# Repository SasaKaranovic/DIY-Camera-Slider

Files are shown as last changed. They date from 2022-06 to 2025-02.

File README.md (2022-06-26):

# DIY WiFi Enabled Camera Slider

## What is this project about?
DIY WiFi Enabled Camera Slider (https://youtu.be/-t66ZylGClk "DIY WiFi Enabled Camera Slider")

Above video shows the finished Camera Slider, how it works, how to build one and motivation behind some of the design decisions.

## How can I build my own?
The above video explains the idea and how hardware and firmware works. It's recommended that you watch that first.
Hardware and firmware build instructions and source files are available in their respective folders.

---

Blog page: https://sasakaranovic.com/projects/diy-camera-slider/

YouTube video: http://www.youtube.com/watch?v=-t66ZylGClk

---

#### Sasa Karanovic

<a href="https://sasakaranovic.com/" target="_blank" title="Sasa Karanovic Home Page"> Home Page</a> &nbsp;&middot;&nbsp;
<a href="https://youtube.com/c/sasakaranovic" target="_blank" title="Sasa Karanovic on YouTube"> YouTube</a> &nbsp;&middot;&nbsp;
<a href="https://github.com/sasakaranovic" target="_blank" title="Sasa Karanovic on GitHub"> GitHub</a> &nbsp;&middot;&nbsp;
<a href="https://twitter.com/_sasakaranovic_" target="_blank" title="Sasa Karanovic on Twitter"> Twitter</a> &nbsp;&middot;&nbsp;
<a href="https://instagram.com/_sasakaranovic_" target="_blank" title="Sasa Karanovic on Instagram"> Instagram</a> &nbsp;&middot;&nbsp;
<a href="https://buymeacoffee.com/sasakaranovic" target="_blank" title="Sasa Karanovic on Buy me a coffee"> Buy me a coffee</a>

[home]: https://raw.githubusercontent.com/SasaKaranovic/common/master/assets/img_home.png "Sasa Karanovic Home Page"
[youtube]: https://raw.githubusercontent.com/SasaKaranovic/common/master/assets/img_youtube.png "Sasa Karanovic YouTube channel"
[github]: https://raw.githubusercontent.com/SasaKaranovic/common/master/assets/img_github.png "Sasa Karanovic on GitHub"
[twitter]: https://raw.githubusercontent.com/SasaKaranovic/common/master/assets/img_twitter.png "Sasa Karanovic on Twitter"
[instagram]: https://raw.githubusercontent.com/SasaKaranovic/common/master/assets/img_instagram.png "Sasa Karanovic on Instagram"
[coffee]: https://raw.githubusercontent.com/SasaKaranovic/common/master/assets/img_coffee.png "Buy me a coffee"

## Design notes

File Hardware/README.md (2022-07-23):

# Driver PCB

We are trying to use off-the-shelf components wherever possible to make this open-source open-hardware project accessible to everyone.
The custom PCB is optional. Manufacturing files are in `Manufacturing files` folder. Source files are in `Altium Source Files` which you could use to modify the design.

## Active BOM

If you decide to build the PCB, you can follow the [Active BOM](https://sasakaranovic.com/activebom/diy-camera-slider.html) to help you visualize where
each component is placed and help during assembly.

## Part list

Below parts you can order online from AliExpress, eBay etc.
Links are provided for reference. Feel free to do your own search and find better quality or price.

- 1x [2020 Aluminium Extrusion](https://www.aliexpress.com/item/33019355789.html)
- 4x [Pulley Wheel](https://www.aliexpress.com/item/4001226933910.html)
- 2x [Stepper Motor](https://www.aliexpress.com/item/4001030722318.html)
- 2x [Stepper Motor Driver](https://www.aliexpress.com/item/10000278156894.html)
- 1x [51104 Axial Ball Bearing](https://www.aliexpress.com/item/32825301161.html)
- 1x [F8-16M Axial Ball Bearing](https://www.aliexpress.com/item/1005001624909472.html)
- 1x [6mm GT2 200mm Closed Loop Timing Belt](https://www.aliexpress.com/item/32868149860.html)
- 1x [6mm Cut-to-Size GT2 Timing Belt](https://www.aliexpress.com/item/1005004103945098.html)
- 2x [GT2 Timing Pulley 6mm 20 teeth](https://www.aliexpress.com/item/32629617890.html)
- 1x [GT2 Idler 6mm](https://www.aliexpress.com/item/32671018751.html)
- 1x [Micro switch / Limit Switch](https://www.aliexpress.com/item/4000638031271.html)

Thanks @Eisbaeeer [1](https://github.com/SasaKaranovic/DIY-Camera-Slider/issues/2)

---
[<- Go back to repository root](../README.md)

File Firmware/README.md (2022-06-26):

# How to build firmware

For our firmware development, we are going to use Arduino. Mainly because it's user friendly, easy to use and
most hobbyists are familiar with it or have already used it. While we could build te same or even more efficient
firmware using C and ESP-IDF, we are going to stick with Arduino and hope that this allows the project to be
more friendly and easier to use/modify by wider DIY/hacker community.

## How can I build/compile firmware?
Arduino has many third party libraries that you can use and also build firmware for many different boards.
However, depending for which board you are building firmware and also which libraries your project (sketch) uses,
you might need to manually install them or download them trough board/library manager.

While above mentioned solution works fine, it can lead to issues like installing the "wrong/different" version
of the library, different board files, "wrong/different" build/upload tools and so on. On top of that, since board files
and libraries are shared, we could install a library or a board file while working on another project that breaks our current project.
Hopefully you can see why this is not so great for open-source open-hardware project where we want everyone to be able to easily
checkout a repository and hit the ground running without spending hours setting up and debugging what library or board files are missing.

Luckily we can automate/avoid this by using a build system like PlatformIO. So below we will have two ways of building
the firmware, one will be "easy" by leveraging PlatformiIO build system, and the other one will be a manual one by using
Arduino IDE and manually searching and downloading all the board/library files.

## - The super easy way - Compile and upload using PlatformIO build system  - 

### 1. Install PlatformIO
Installing PlatformIO CLI is pretty straight-forward and also well documented for Windows, Linux and MacOS.
You will need to follow few steps and get PlatformIO CLI installed, detailed tutorial can be found at https://platformio.org/install/cli
Make sure to install [PlatformIO Core](https://docs.platformio.org/en/latest//core/installation.html#installation-methods 'https://docs.platformio.org/en/latest//core/installation.html#installation-methods') and allso that it is available trough [shell](https://docs.platformio.org/en/latest//core/installation.html#piocore-install-shell-commands 'PlatformIO Core - Install Shell Commands¶').

### 2. Build firmware
Open shell/command-prompt and navigate to 'Firmware/platformio' folder.
1. Compile the firmware by typing `pio run`, PlatformIO will download all the required board files and libraries and finally compile the firmware.
2. Upload the firmware with `pio run --target upload --upload-port <COM-PORT>`. Make sure to replace `<COM-PORT>` with your ESP32's COM port (ie COM1 or /dev/ttyACM0)
3. Upload the file system (Web page) with `pio run --target uploadfs --upload-port <COM-PORT>`, again replace `<COM-PORT>` with your ESP32's COM port.

Every time you make a firmware change, you need to run steps #1 and #2.
Every time you make a change to the web page (anything inside `data` folder) you only need to run step #3.

## - The less easy way - Compile using Arduino IDE and manually install all board files and libraries

### 1. Install Arduino IDE
Download and install Arduino IDE from https://www.arduino.cc/en/software

### 2. Install ESP32 board files
Add ESP32 board files to you Arduino IDE
1. Go to `File -> Preferences`
2. Find `Additional Board Manager URLs:` and add `https://dl.espressif.com/dl/package_esp32_index.json`
3. Go to `Boards -> Board manager`.
4. Search for `esp32`.
5. Find a board package title `esp32 -> by Espressif Systems` and install it.
(Currently we are using version 1.0.6, in case you have any issues, try installing this exact version)

### 3. Install libraries used by the project
Install third party libraries that required
1. Go to `Sketch -> Include Library -> Manage Libraries... (CTRL+SHIFT+I)`
2. Find libraries from the list below and install them one by one

- AsyncTCP
- ESPAsyncWebServer
- FlexyStepper
- ESPmDNS

### 4. Install some more libraries
You will manually have to install following libraries.
One way is to create a `Libraries` folder in your sketch folder. Then download the libraries and place them in Libraries folder.

- https://github.com/me-no-dev/AsyncTCP
- https://github.com/me-no-dev/ESPAsyncWebServer
- https://github.com/Stan-Reifel/FlexyStepper
- https://github.com/espressif/arduino-esp32/tree/master/libraries/ESPmDNS

### 5. Select build board
You need to tell Arduino IDE for which board we want to build the firmware.
Go to `Tools -> Board: -> ESP32 Arduino` and select `ESP32 Dev Module`
Go to `Tools -> Port` and select your ESP32 COM port

### 6. Compile and upload the firmware
You need to compile and upload firmware.
Go to `Sketch -> Upload`
You will need to do this step every time you make a change to the firmware.

### 7. Upload the file system
You need to tell Arduino IDE which partition scheme we want to use
Go to `Tools -> Partition Scheme` and select `1MB APP / 3MB SPIFF`
Now you can go upload file system trough `Tools -> ESP32 Sketch Data Upload` menu item.
If you are missing above menu item, you will need to manually install [ESP32 Sketch Data Upload tool](https://github.com/me-no-dev/arduino-esp32fs-plugin).
You will need to do this step every time you make a change to the web page (or anything inside the data folder)

[<- Go back to repository root](../README.md)

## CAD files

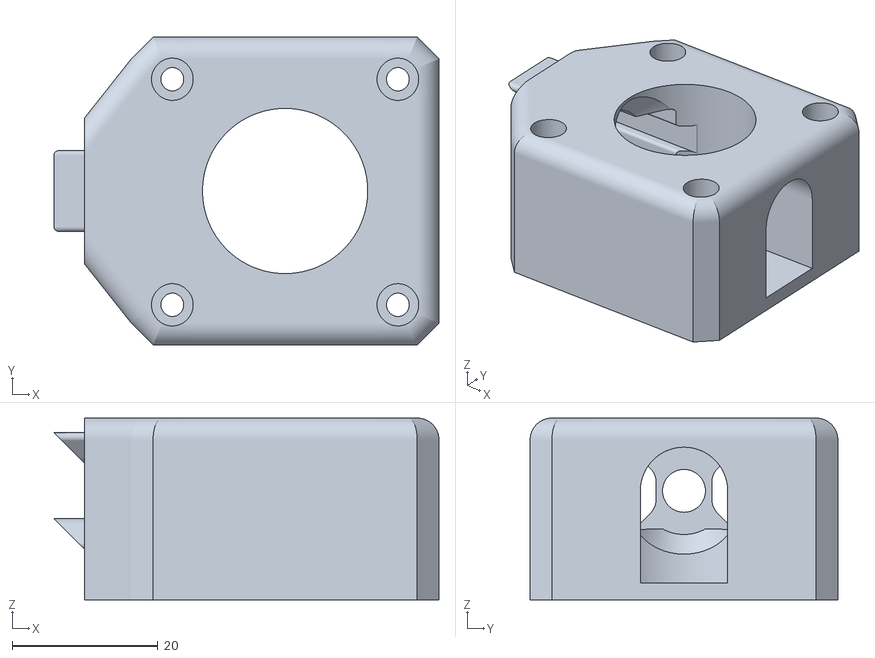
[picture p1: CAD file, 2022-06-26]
3D CAD/STEP/Motor-Mount.stl
52.9 x 42.3 x 25.0

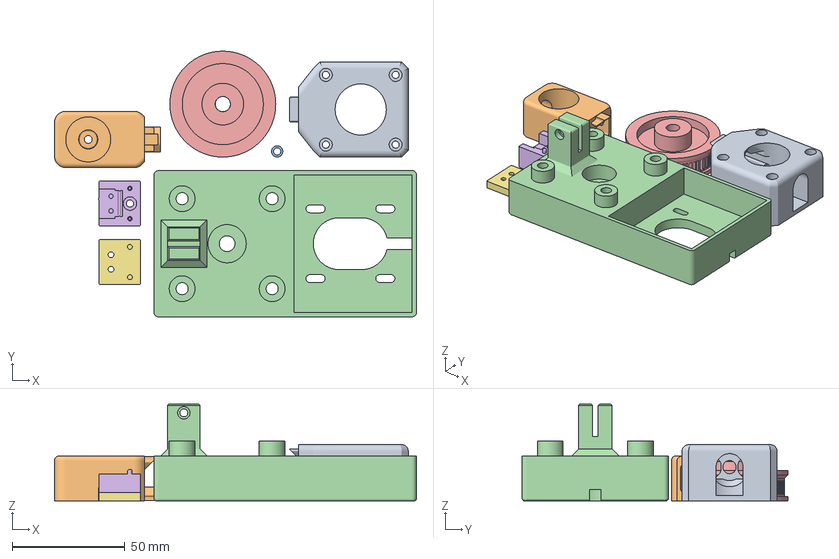
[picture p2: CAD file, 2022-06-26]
3D CAD/STEP/2020_CameraSlider.3mf
160.9 x 118.1 x 43.0 mm
Motor-Mount.stl
Idler Mount.stl
Idler_M3_Spacer.stl
Rotating_Platform_Base.stl
Rotating-Base.stl
Limit_Switch_Mount_Bottom.stl
Limit_Switch_Mount_Top.stl

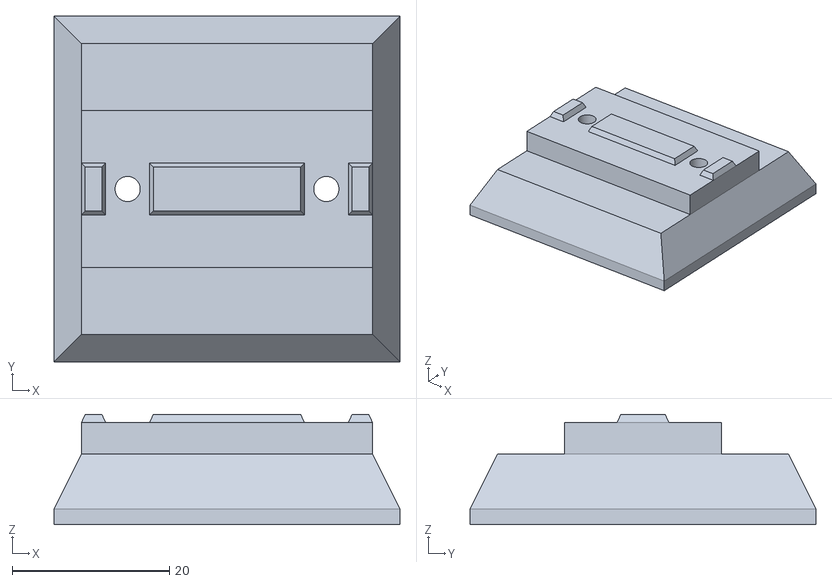
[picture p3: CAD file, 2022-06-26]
3D CAD/STEP/Tripod-Mount.stl
44.0 x 44.0 x 14.0

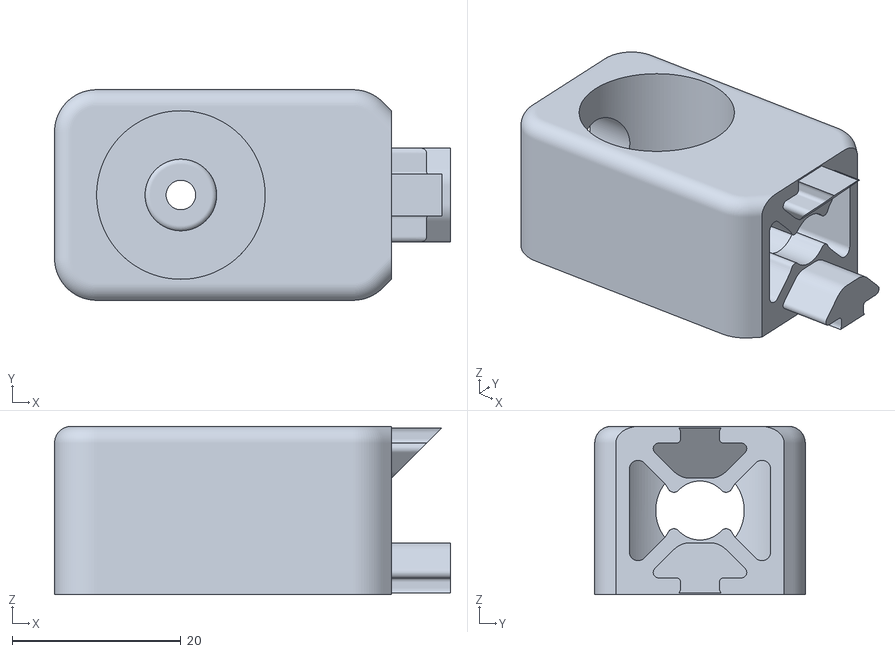
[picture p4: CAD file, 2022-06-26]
3D CAD/STEP/Idler Mount.stl
47.0 x 25.0 x 20.0

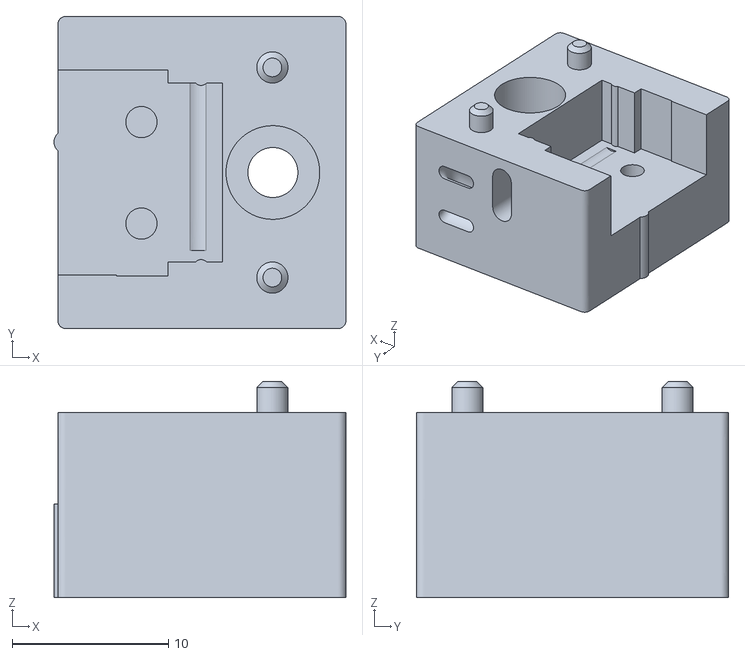
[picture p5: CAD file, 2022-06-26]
3D CAD/STEP/Limit_Switch_Mount_Bottom.stl
18.7 x 20.0 x 13.9

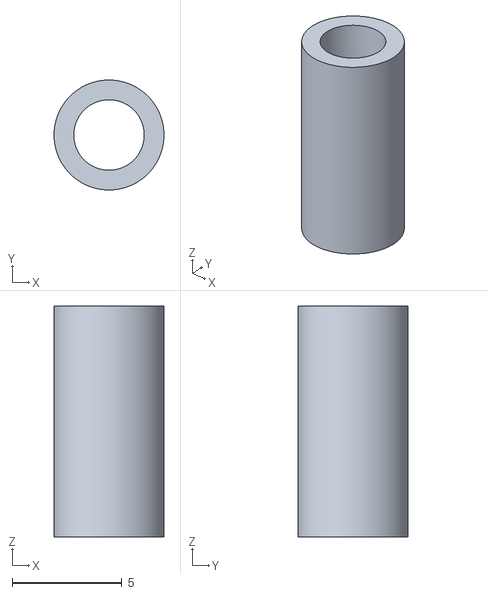
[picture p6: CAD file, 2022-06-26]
3D CAD/STEP/Idler_M3_Spacer.stl
5.00 x 5.00 x 10.5

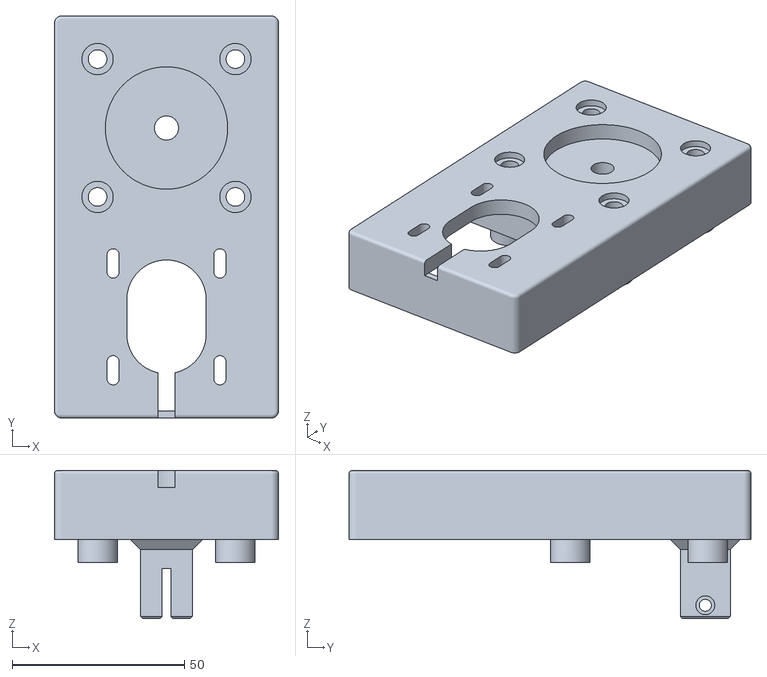
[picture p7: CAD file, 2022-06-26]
3D CAD/STEP/Rotating_Platform_Base.stl
65.0 x 116.7 x 43.0

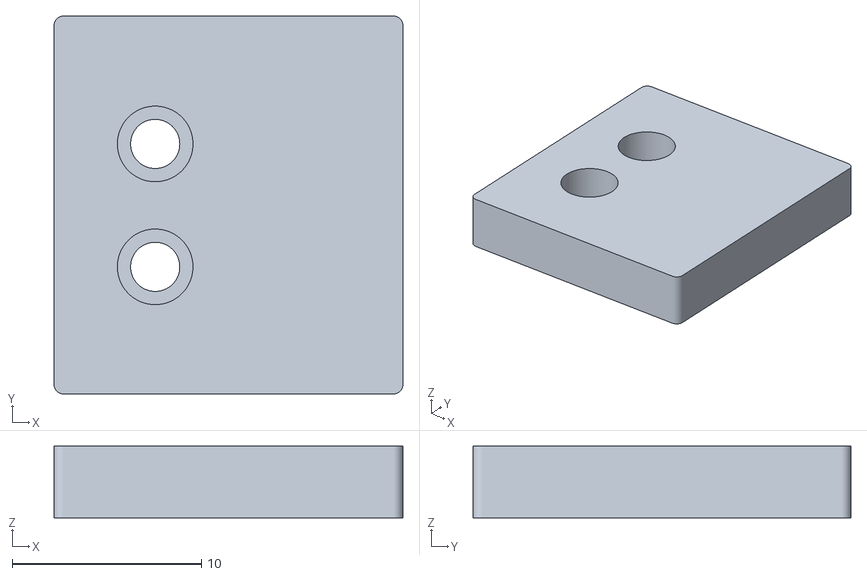
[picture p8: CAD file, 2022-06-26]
3D CAD/STEP/Limit_Switch_Mount_Top.stl
18.5 x 20.0 x 3.80

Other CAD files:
3D CAD/DIY-Camera-Slider-2020 v37.f3z

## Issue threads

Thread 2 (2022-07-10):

Wrong BOM part list

Eisbaeeer, 2022-07-10:
Hi Sascha
https://github.com/SasaKaranovic/DIY-Camera-Slider/tree/master/Hardware#part-list

Wrong:
1x [6mm GT2 280mm Closed Loop Timing Belt]
Correct:
1x[6mm GT2 200mm Closed Loop Timing Belt]

Wrong:
2x [GT2 Idler 6mm]
Correct:
1x [GT2 Idler 6mm]

ghtomcat, 2022-07-16:
Also, it would help to link where to buy the endswitch

Eisbaeeer, 2022-07-16:
> And which bore the idler has (3mm or 5mm).
The idler in project has 3mm. I used standard 5mm and drilled up from 3 to 5.
You have to set the right hight with spacer.
Endswitches are the small one from e.g. Omron like D2FC.
Hope that helped!

ghtomcat, 2022-07-18:
@Eisbaeeer thanks for your help! I printed all the 3D Parts and now i'm waiting for the other parts to arrive

SasaKaranovic, 2022-07-23:
Thanks @Eisbaeeer !
The 280mm was used in the "old" version that uses 2040 aluminum extrusion instead of 2020. Good catch, changed it to 200mm.
And you are right, it's just one GT2 pulley.

@ghtomcat I believe the pulley I had laying around was 5mm bore and since I'm using 3mm screw I had to 3D print a tiny "sleeve" to keep pulley centered. If 3mm screw fits trough the 3mm pulley then I would say go with that.
Good catch! I have updated the BoM to include end-switch. Also I would love to see how your camera slider turns out!

thijstriemstra, 2023-04-12:
> Good catch, changed it to 200mm.

perhaps this ticket can be closed then.

Closed 2023-04-14.

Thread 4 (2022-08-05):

Pulley issue

ghtomcat, 2022-08-05:
Do i have the wrong pulleys or the wrong extrusion? Somehow the two do not fit :(

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

buttim, 2022-08-23:
for my experience you might need to loosen the screws that fix the pulleys a bit. It might depends on your printer's tolerance too

ghtomcat, 2022-08-24:
Thank you @buttim, i will try that and report back

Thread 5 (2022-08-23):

Wifi keeps disconnecting

buttim, 2022-08-23:
The wifi connect loop never ends. The return value from `WiFi.begin()` is always 6 (`WL_DISCONNECTED`).
I solved this issue changing the code in _DIY_CameraSlider.ino_ like this:
from
`` WiFi_status = WiFi.begin(ssid, password);``

to
``
WiFi.begin(ssid, password);
WiFi_status = WiFi.waitForConnectResult();``

thijstriemstra, 2023-05-16:
thanks. the begin can/should also be moved out of the while loop:

```c++
WiFi.begin(ssid, password);

while (WiFi_status != wl_status_t::WL_CONNECTED)
{
    Serial.print("Connecting to SSID: ");
    Serial.println(ssid);
    WiFi_status = WiFi.waitForConnectResult();
}
```

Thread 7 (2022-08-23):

Use WiFiManager instead of hard wired AP user/password

buttim, 2022-08-23:
This is easy and would even allow binary distribution of the firmware (no need for Arduino IDE installation and recompilation).

I gave it a try and it should be enough to do the following modifications to DIY_CameraSlider.ino_:
1. Replace `#include "config_wifi.h"` with #include` <WiFiManager.h>`
2. Add the declaration `WiFiManager wifiManager;` after all the includes
3. Remove the whole `while` after the comment `// Connect to WiFi`
4. Add in its place the single line `wifiManager.autoConnect("DIY_CameraSlider", "cameraslider");`

The file _config_wifi.h_ can then be removed

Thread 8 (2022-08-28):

The software is very easy to use, but it is not convenient to connect different WiFi

Qigaoo, 2022-08-28:
If there is no WiFi outside, what can I do to control the operation of the device with my mobile phone? Or what should I do if I often use it in a different place?

buttim, 2022-08-28:
Set up you phone as a Wifi access point

buttim, 2022-09-12:
Also consider modifying the Arduino code as I suggested here: https://github.com/SasaKaranovic/DIY-Camera-Slider/issues/7

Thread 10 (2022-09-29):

Question about power

leeeboo, 2022-09-29:
Is the esp32 also powered from a dc-dc out? If I'm not mistaken then out should be 12v and esp32 should be 5v. am I missing something here? Thanks!

thijstriemstra, 2023-05-16:
I had the same question, and got this [response](https://www.printables.com/model/232492-diy-camera-slider/comments/799867):

> The LM2596 should be set to the voltage you want on your motors (for my setup the sweet spot between torque and noise was around 8V). The ESP32 has built in voltage regulator that should take care of regulating voltage for ESP32.

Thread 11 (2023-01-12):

Connecting for the first time

andeecollard, 2023-01-12:
Hi,
I think I've done everything. It's compiled with my WIFI credentials. What do I type into the web browser to find the web app?
Thanks

andeecollard, 2023-01-14:
Figured this out— platformio through terminal is the way to go. The ip can then be seen in arduino serial monitor. The next problem is I can’t get anything to move. I’ve tried a cheap arduino cnc shield and an mks dlc32 v2 with A4988 drivers. I haven’t changed anything in the code apart from the Wi-Fi credentials. Anyone have any advice?

getsetbro, 2024-01-11:
Also you can view it at http://sk_camera_slider.local

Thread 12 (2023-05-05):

Stepper driver replacement

leandromatos, 2023-05-05:
Can I replace the driver from DRV8825 with TMC2209? If yes, do I need to change something on the PCB?

Closed 2023-06-05.

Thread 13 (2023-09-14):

WebServer issue

patrickschoenherr, 2023-09-14:
The ESP is connected to my router but I'm not able to open the web interface.

While compiling the code in Platform.Io in VSCode I get the following problems:

[{
	"resource": "/c:/Daten/Home Assistant/DIY Camera Slider/DIY-Camera-Slider-master/Firmware/src/DIY_CameraSlider.ino",
	"owner": "C/C++: IntelliSense",
	"code": "20",
	"severity": 8,
	"message": "identifier \"setupWebServer\" is undefined",
	"source": "C/C++",
	"startLineNumber": 108,
	"startColumn": 2,
	"endLineNumber": 108,
	"endColumn": 16
}]

How can I solve this?

getsetbro, 2024-01-11:
@patrickschoenherr You might need to click Build Filesystem Image and then Upload Filesystem Image to get the web app files on the device.
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

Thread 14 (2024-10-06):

Hardware issues (holes not pth, no logic power for driver)

nicohofdtz, 2024-10-06:
I have some major issues with my build.

**Issue 1: Holes not plated**
When I received my PCBs I noticed most holes were not plated-through. I first suspected a manufacturing error but the Altium files showed the issue in the design:
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
The pth holes are highlighted.
Actually all holes should be pth for the design to work. I worked around the issue by soldering at the top of the PCB.

**Issue 2: No logic power for stepper drivers**
I then found that the stepper drivers are not supplied with logic power. That seems to work for the DRV8825 but it doesn't work for the A4988. I solved this issue by adding some wires.

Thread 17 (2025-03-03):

Unable to compile for an "ESP32Dev" module

BullzLabz, 2025-03-03:
### Hello @SasaKaranovic ,

Firstly, thank you for this project and thank you for your help.

As described in your [BOM list](https://sasakaranovic.com/activebom/diy-camera-slider.html) and in your [Youtube video](https://youtu.be/-t66ZylGClk), I use an "ESP32" module, more precisely **ESP32-WROOM-32D**.

Following our exchanges by email, I tried to compile the project with the last two versions that you kindly updated but without success. I obviously took care to change the card type by replacing **"esp32-c3-devkitm-1"** with **"esp32dev"**.

I would like to understand where the error comes from but unfortunately my skills with "PlateformIO" and the Arduino code of your project are very limited. I searched, tested, searched again, tested again and retested but nothing works, impossible to compile your latest version with LittleFS.

Luckily, I managed to compile the old version of your project with this "platformio.ini".

```
; PlatformIO Project Configuration File
;
;   Build options: build flags, source filter
;   Upload options: custom upload port, speed and extra flags
;   Library options: dependencies, extra library storages
;   Advanced options: extra scripting
;
; Please visit documentation for the other options and examples
; https://docs.platformio.org/page/projectconf.html

[platformio]
default_envs = esp32dev

[env:esp32dev]
board_build.f_cpu = 240000000L
board_build.f_flash = 40000000L
board_build.flash_mode = dio
board_build.partitions = noota_3g.csv

framework = arduino
platform = espressif32@3.5.0
board = esp32dev
upload_protocol = esptool
Monitor_speed = 115200

lib_deps=
    SPI @ 2.0.0
    SPIFFS
    FS @ 2.0.0
    WiFi @ 2.0.0
    https://github.com/SasaKaranovic/ESPAsyncWebServer.git @ 1.2.3
    zeed/AsyncTCP
    FlexyStepper @ 1.0.0
    ESPmDNS @ 2.0.0
```

Could you help me understand and compile the latest version of your project please, because even if I manage to compile your latest version without changing anything in your "platformio.ini", when uploading the project to the **ESP32**, the terminal tells me that it is impossible because it is not the right module **"esp32-c3-devkitm-1"**.

I think that people who will try to compile the project by following your [BOM list](https://sasakaranovic.com/activebom/diy-camera-slider.html), by watching your [Youtube video](https://youtu.be/-t66ZylGClk) and especially by having completely soldered the PCB with all the components will find themselves blocked because it does not match the **ESP32dev** module.

Thank you for making this project available, and for taking the time to exchange by email to try to solve my problem.

Kind regards
BullzLabz

SasaKaranovic, 2025-03-03:
Hey @BullzLabz

If you have a `platformio.ini` that successfully compiles the code. You can simply change the board from `esp32-c3-devkitm-1` to `esp32dev` or whichever board/module you are using. The full list of boards is listed on the official [platformio docs](https://docs.platformio.org/en/latest/boards/#espressif-32) page.

The difference between the two version of the code that you mentioned is that one uses SPIFF and the other uses LittleFS.
So the difference is purely "under the hood" change that you will probably not notice anyway.

With that said, I would recommend using whichever version you are comfortable compiling on your system.

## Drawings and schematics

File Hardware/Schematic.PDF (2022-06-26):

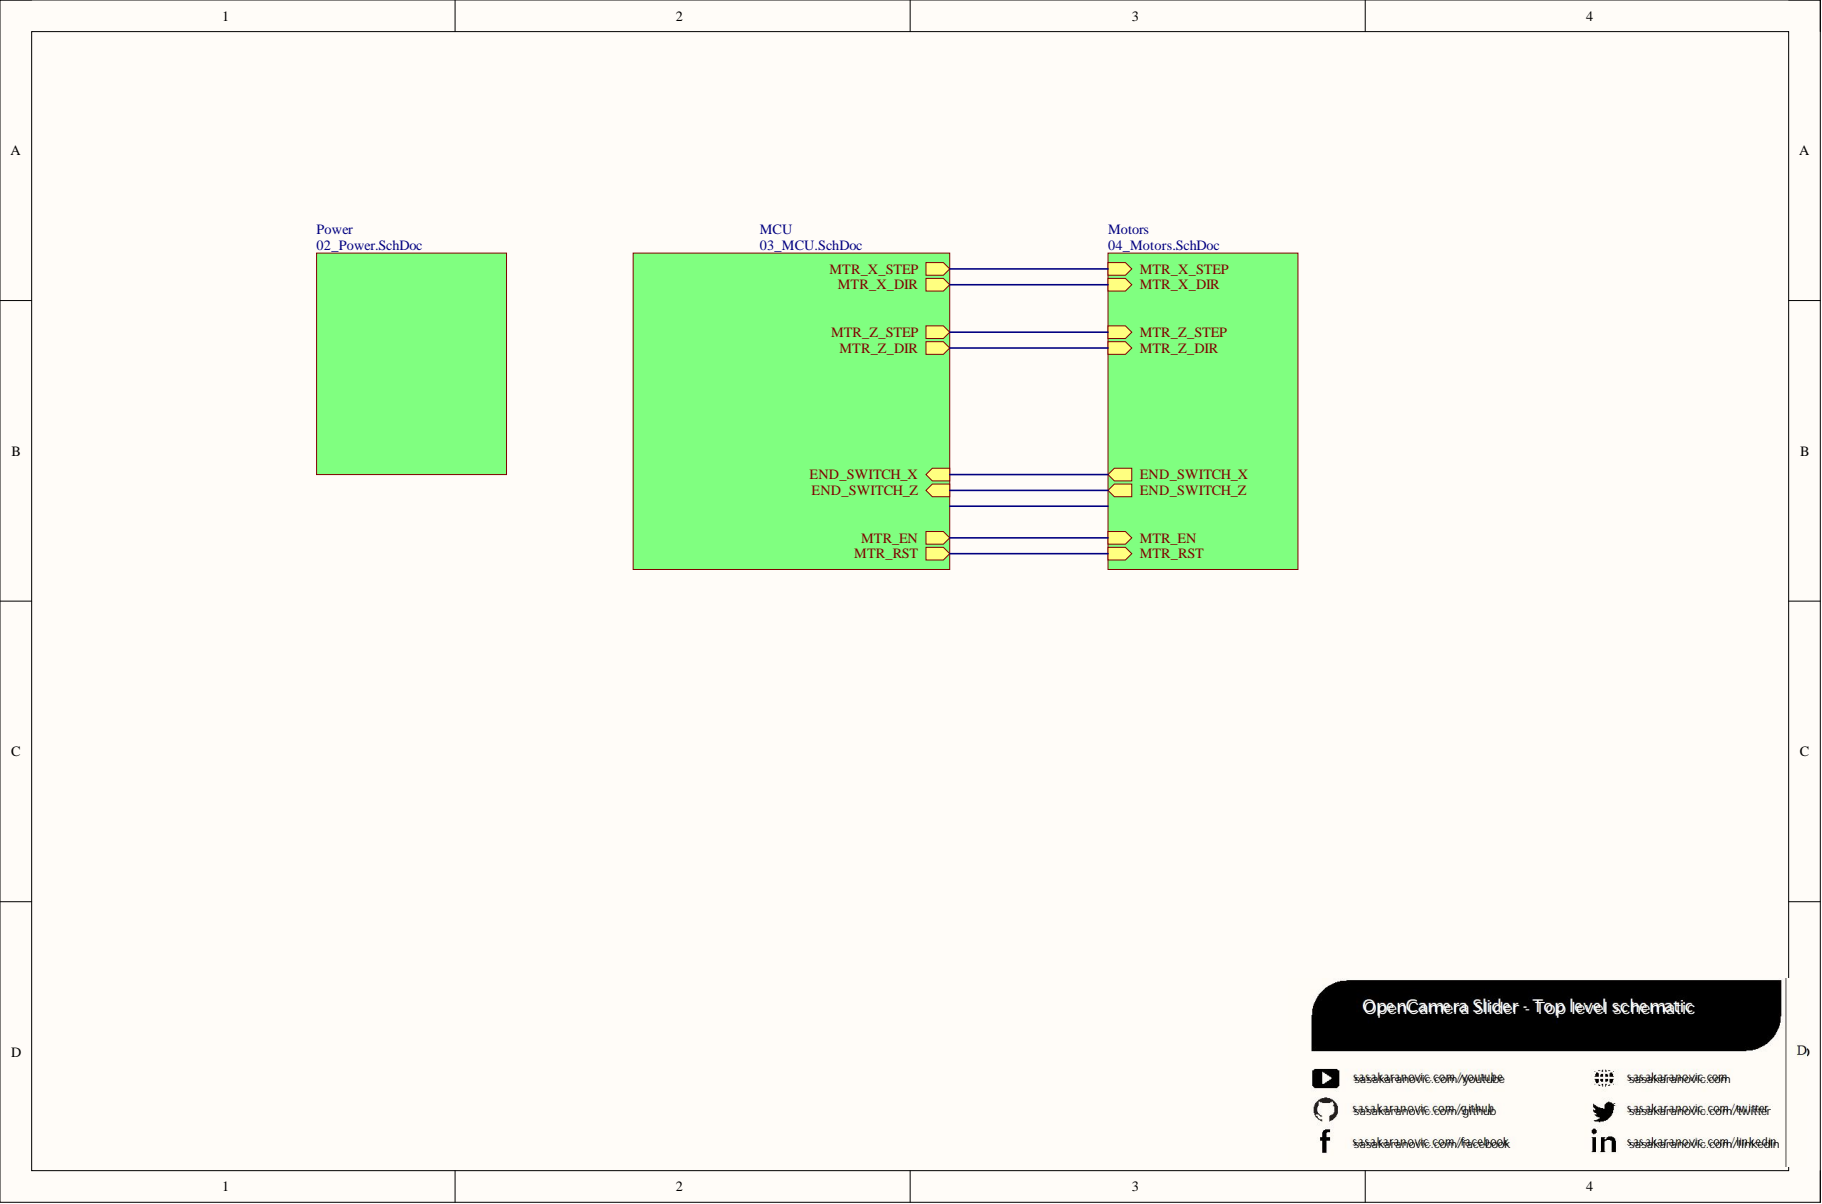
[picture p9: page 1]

OpenCamera Slider - Top level schematic

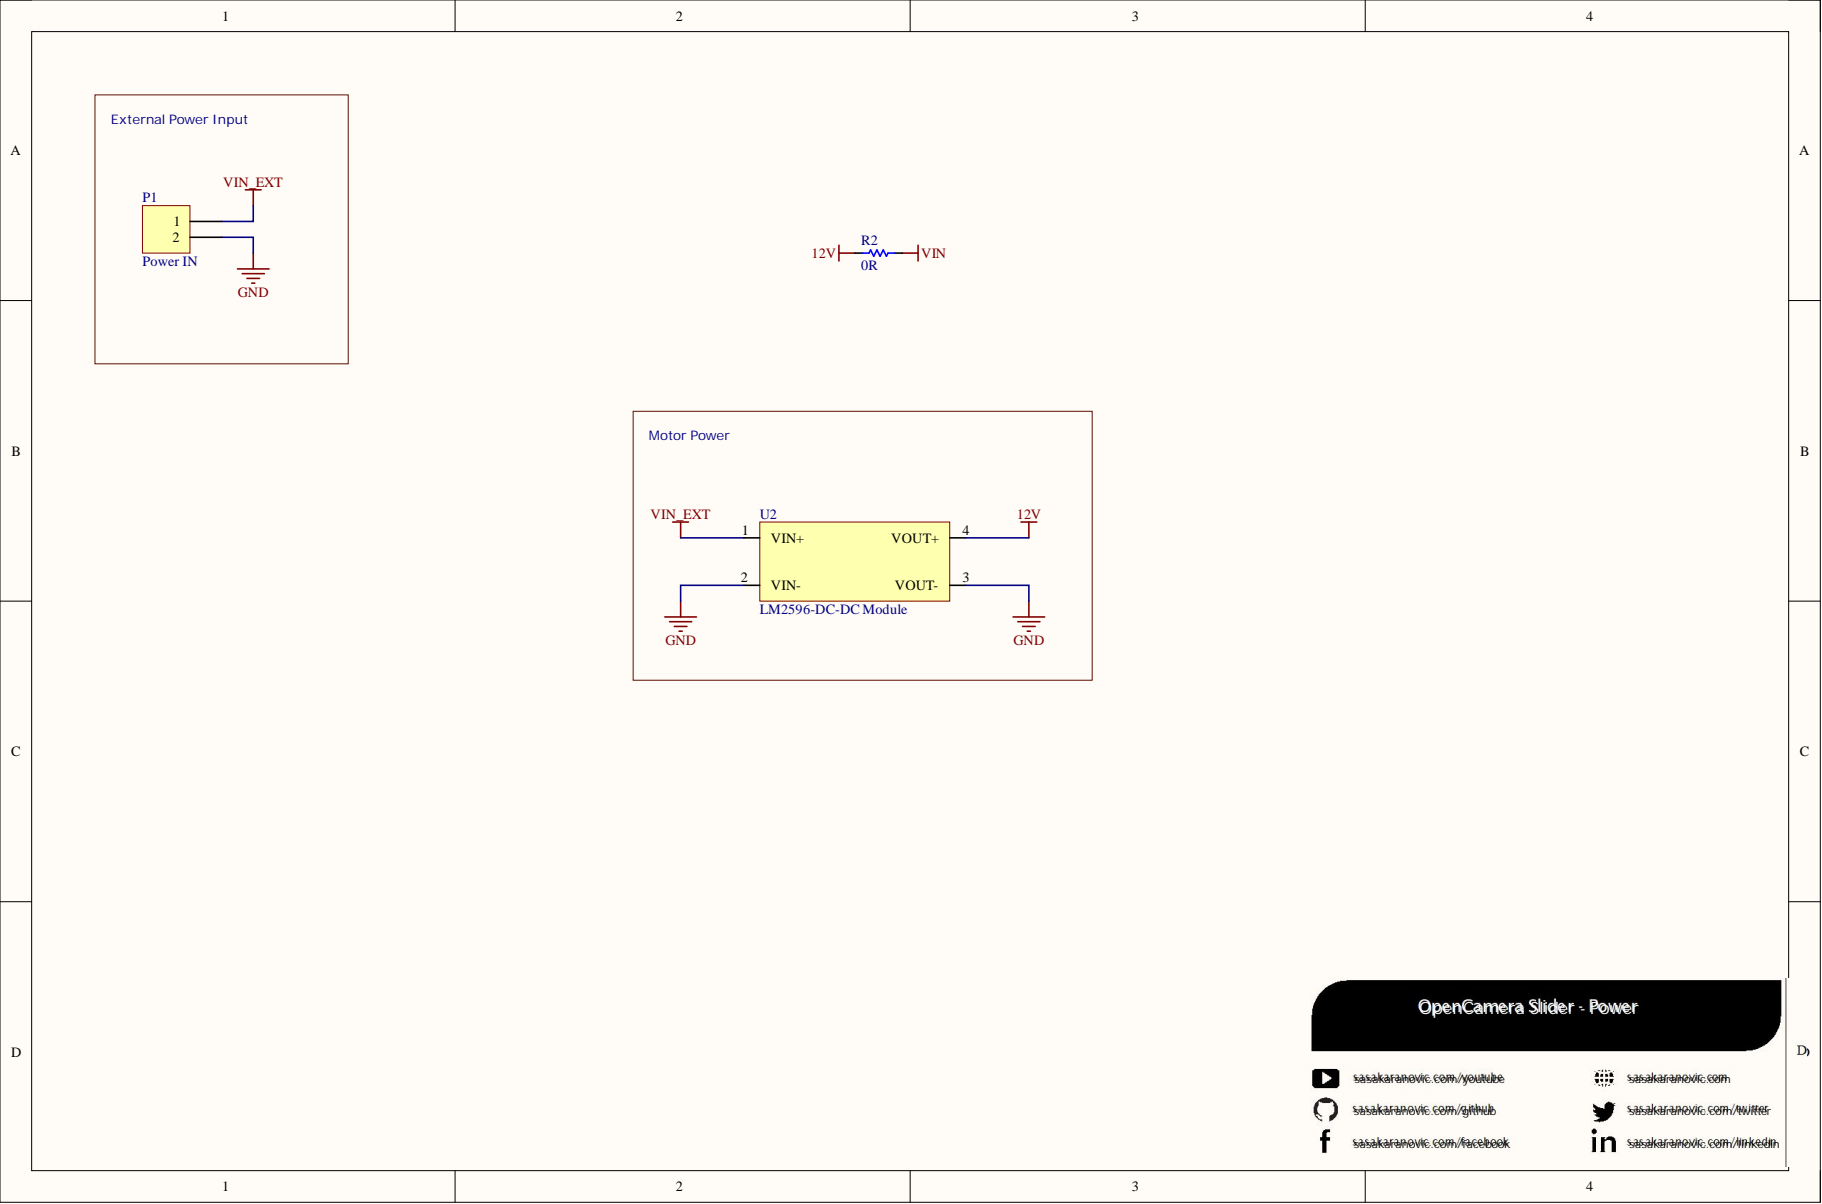
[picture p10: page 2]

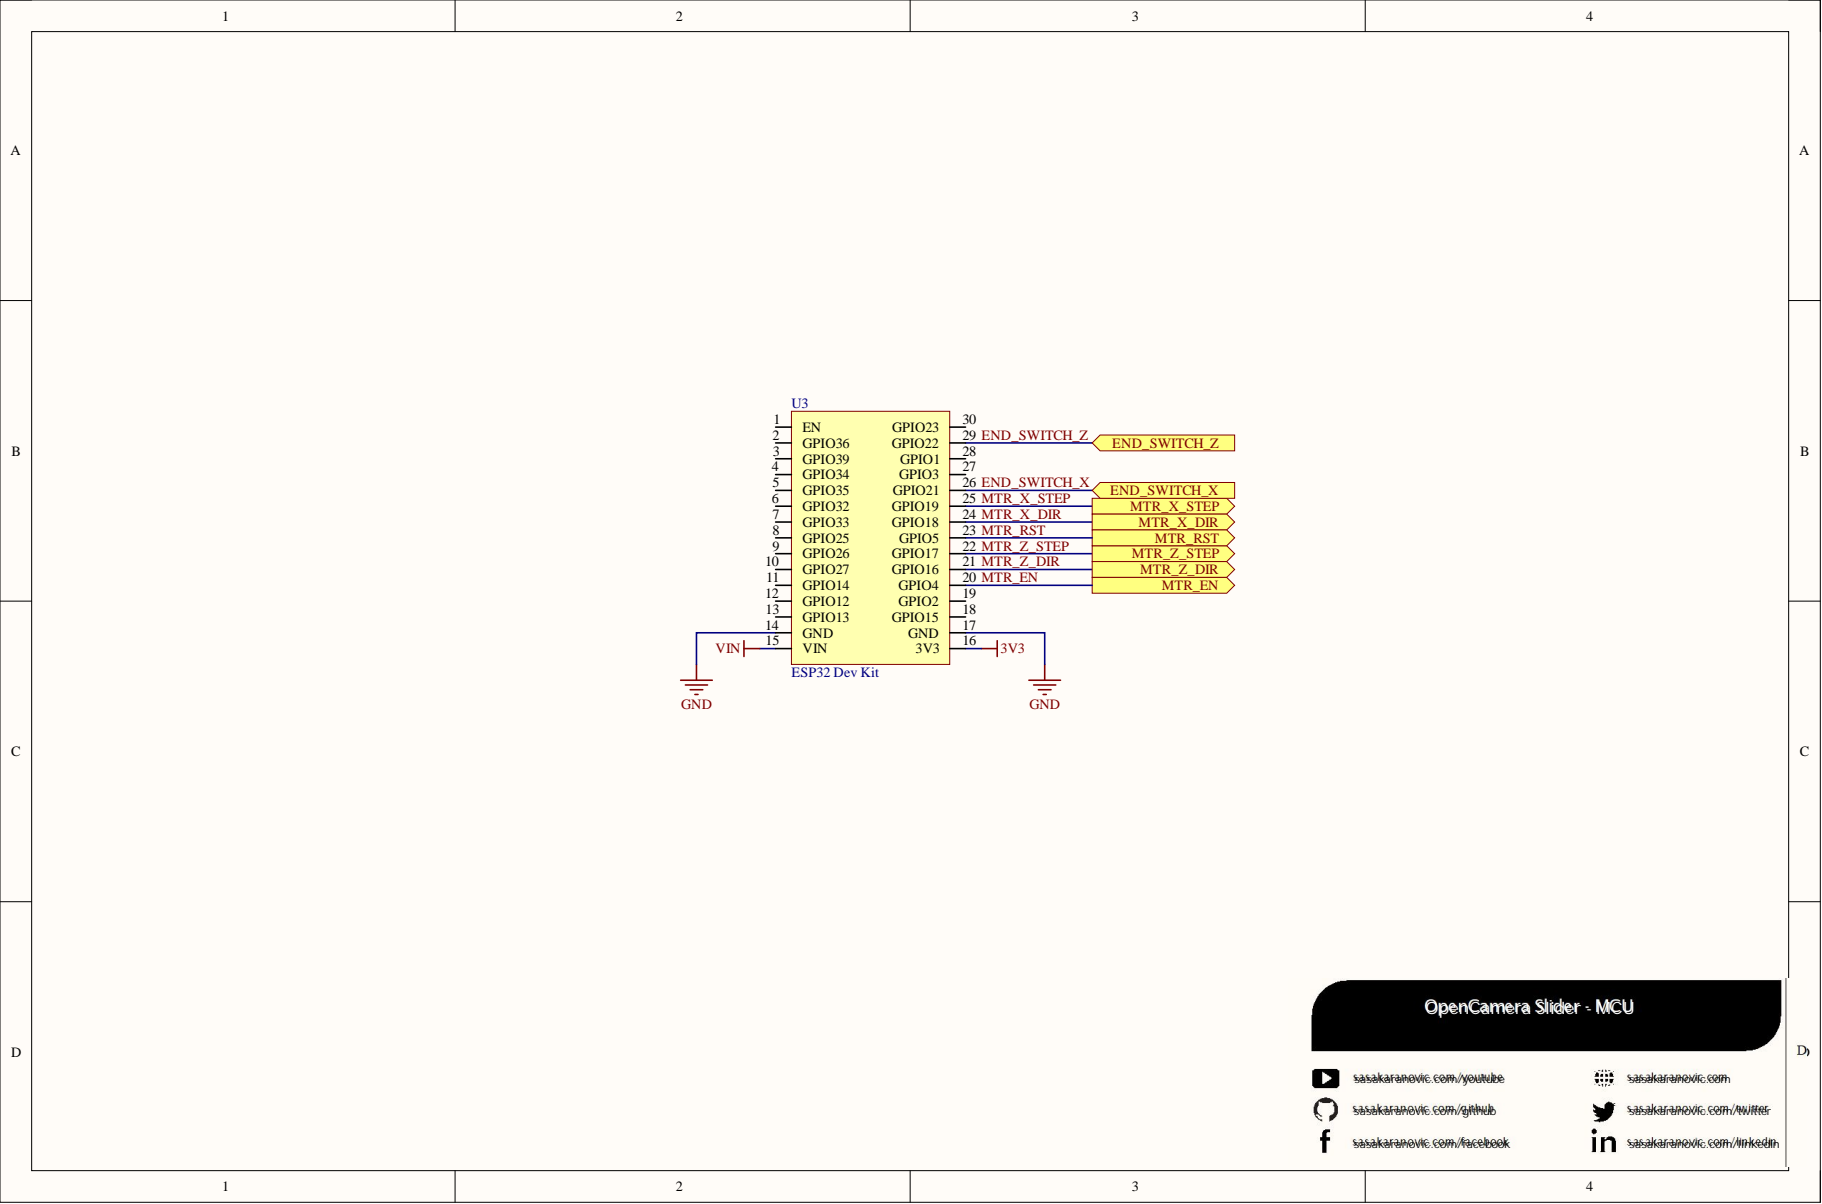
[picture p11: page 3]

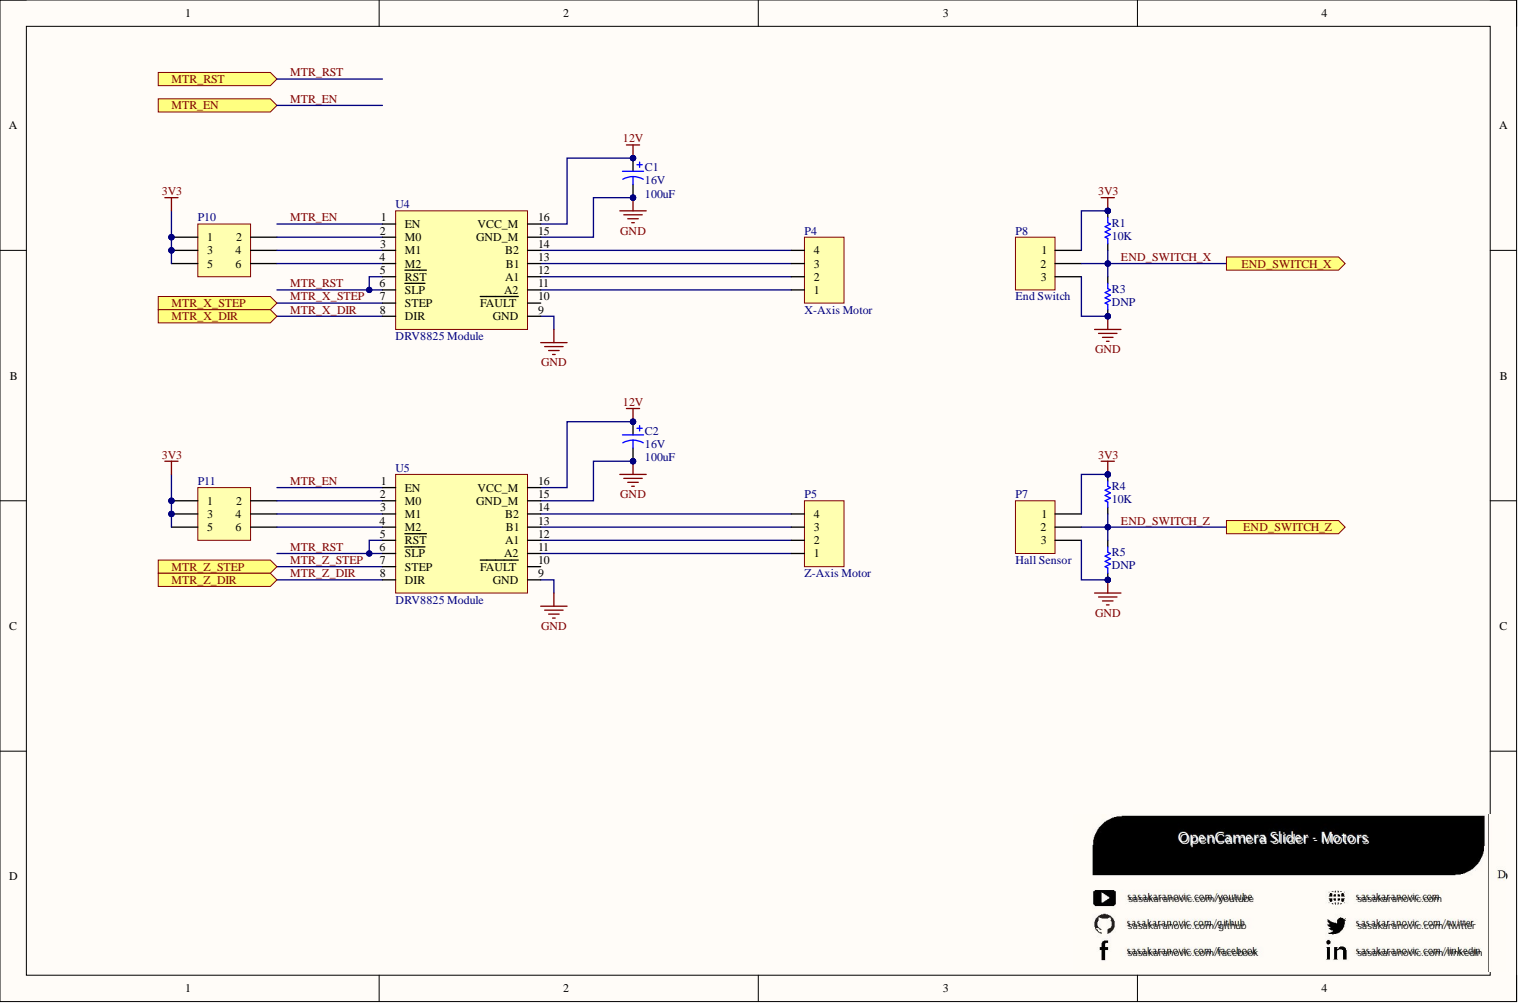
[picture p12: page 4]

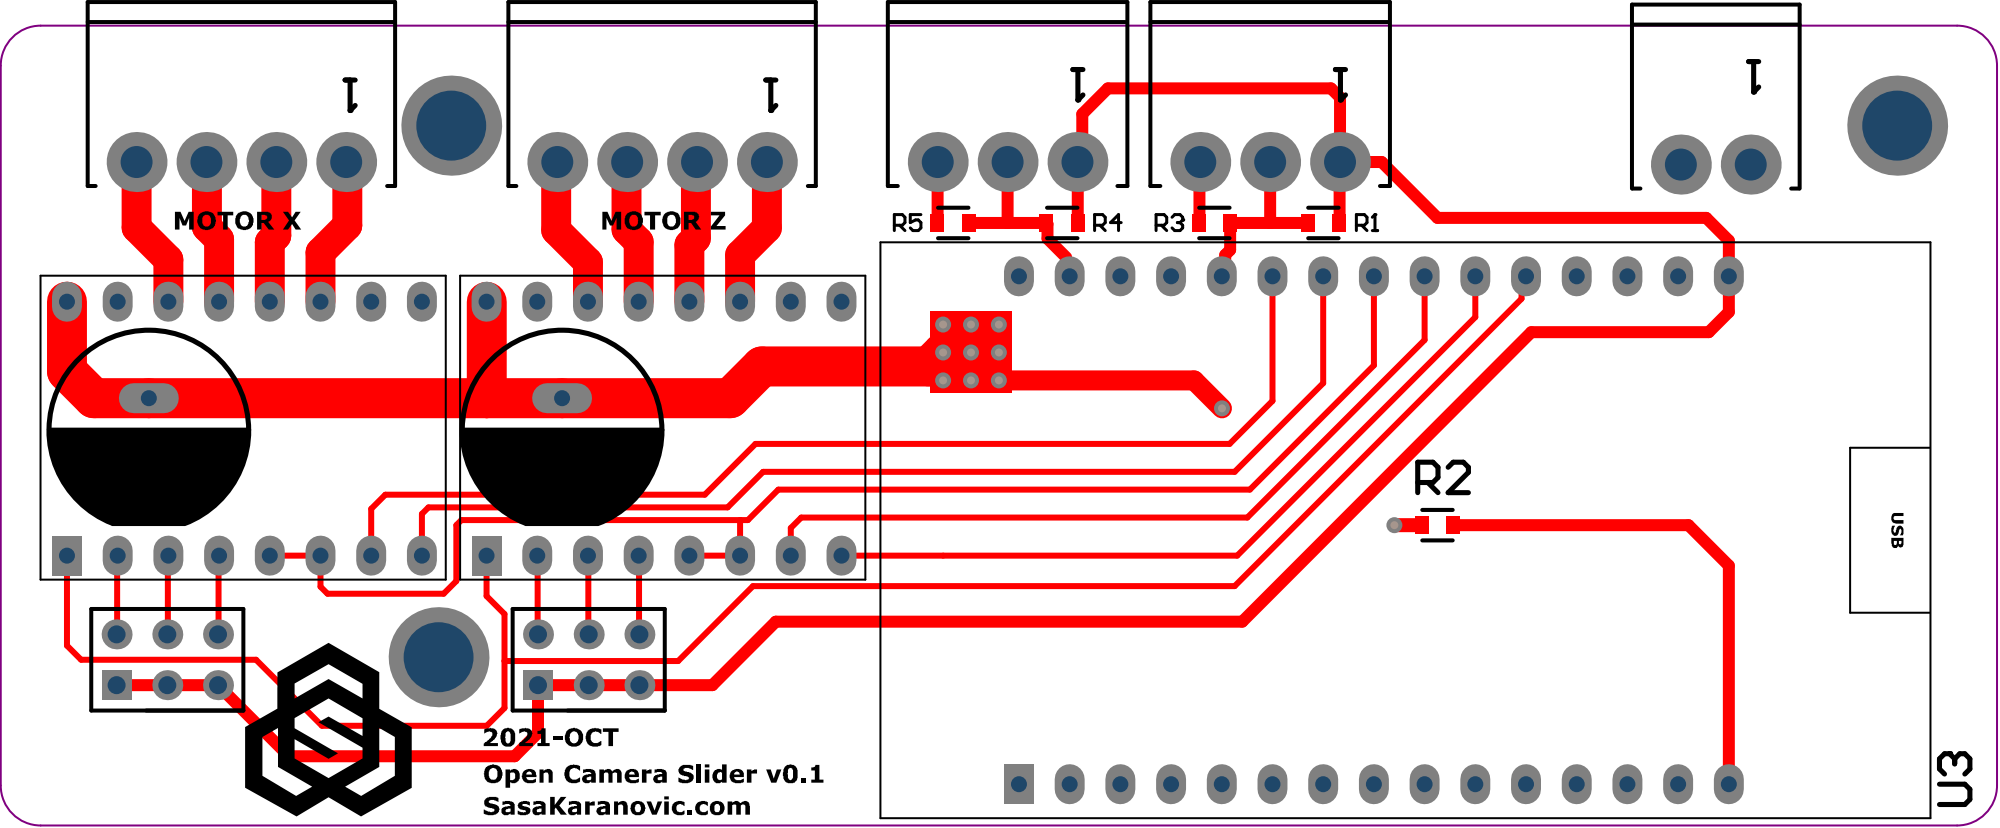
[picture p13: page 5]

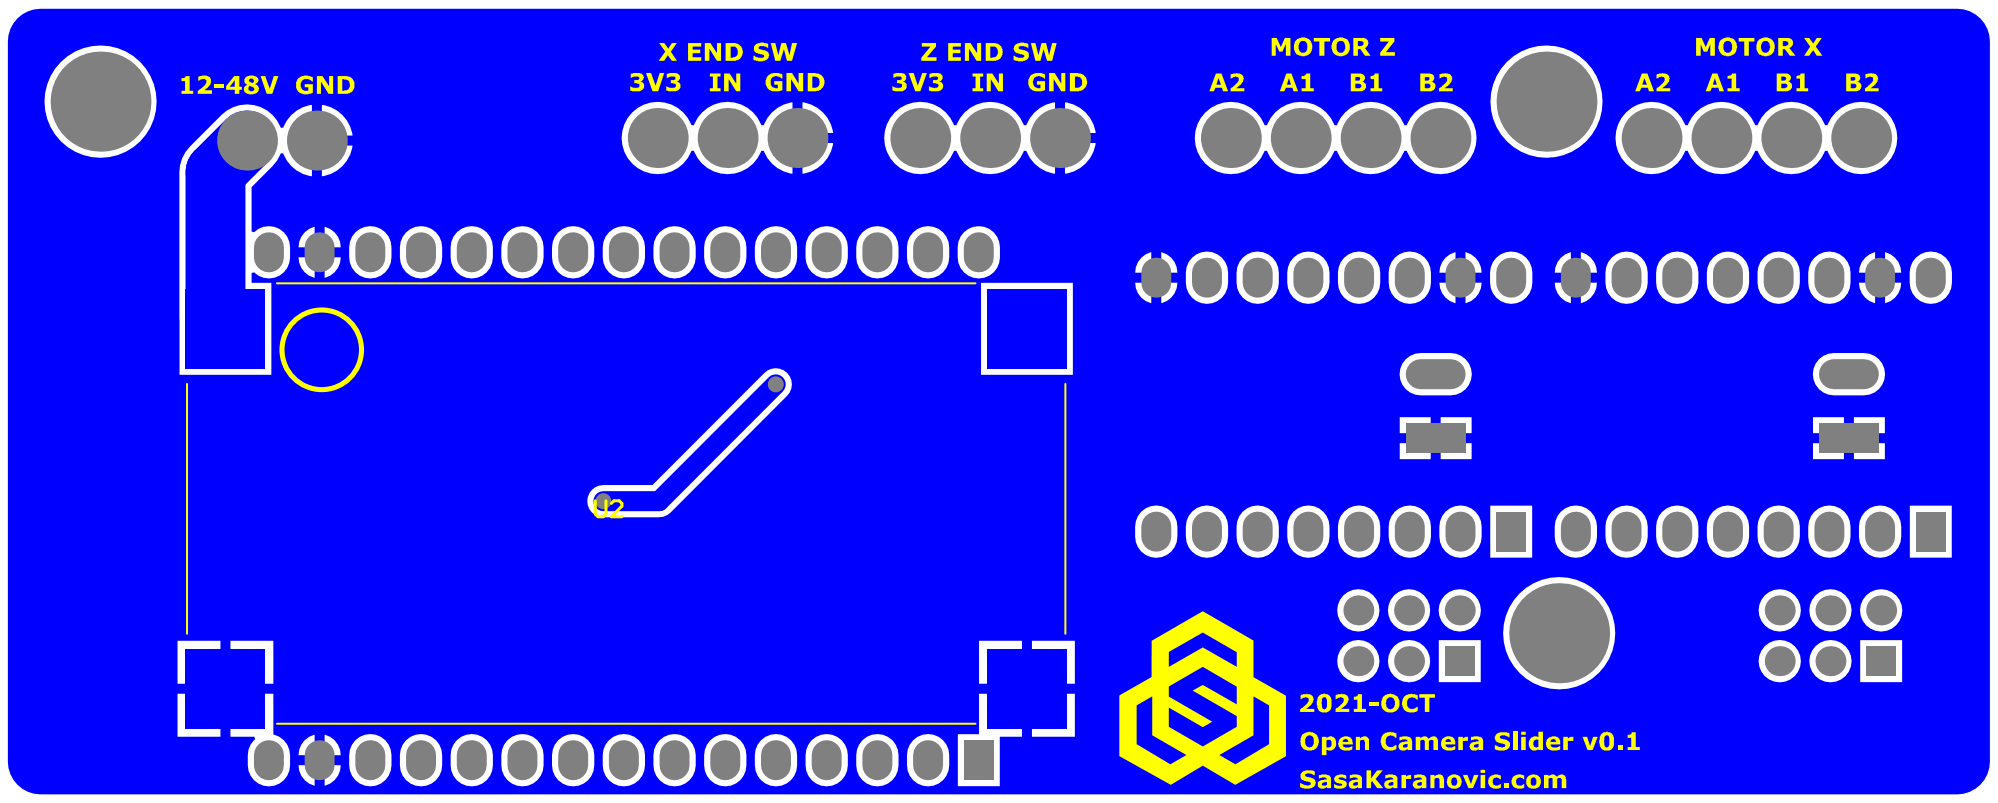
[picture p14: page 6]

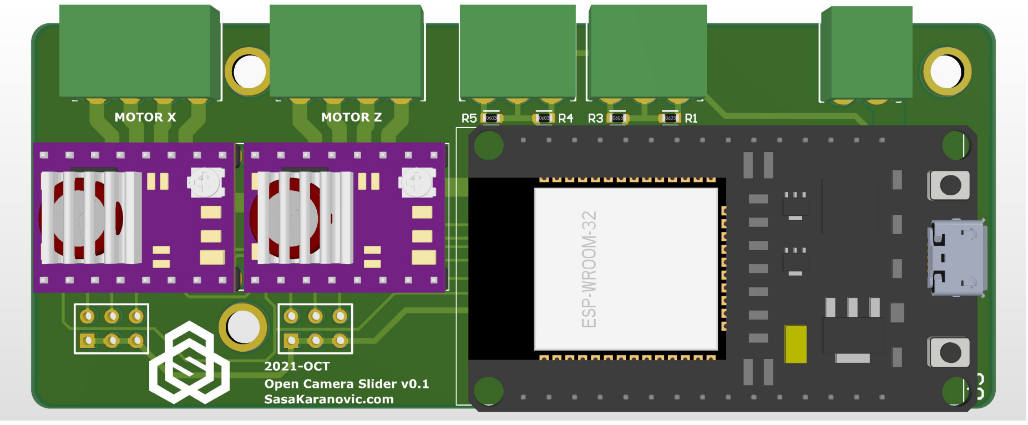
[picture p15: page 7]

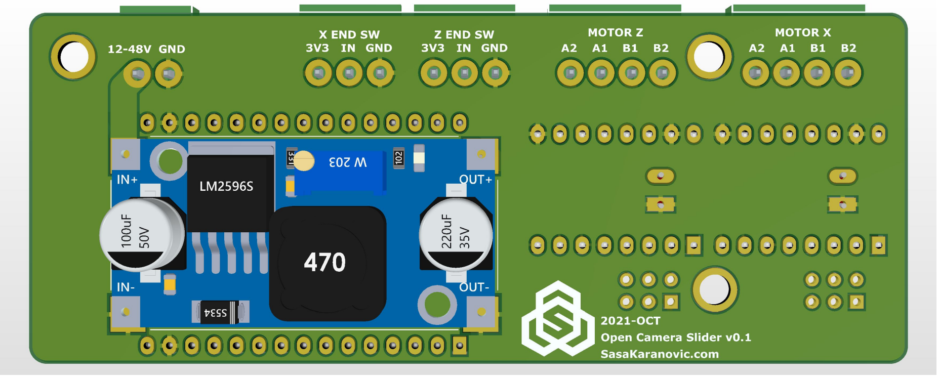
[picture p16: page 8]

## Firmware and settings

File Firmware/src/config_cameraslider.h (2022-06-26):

#ifndef __CAMERASLIDER_CFG__
#define __CAMERASLIDER_CFG__

// Configure oTA
#define MDNS_NAME       "sk_camera_slider"
#define OTA_NAME        "sk_camera_slider"
#define OTA_PASSWORD    "change_this_please"

// Various GPIO connections to control motor direction
// enable/disbale, reset, end/limit switch etc.
#define PIN_MOTOR_X_STEP			19
#define PIN_MOTOR_X_DIR             18
#define PIN_MOTOR_Z_STEP            17
#define PIN_MOTOR_Z_DIR             16
#define PIN_MTR_nRST                5
#define PIN_MTR_nEN                 4
#define PIN_LED 					2
#define PIN_END_SWICH_X			    21


// "Mechanical" configuration of the camera slider
#define RAIL_LENGTH_MM			    330       // Rail (2020 extrusion) length that platform can slide along (in milimeters)
#define SLIDE_STEPS_PER_MM          187
#define MIN_STEP_SLIDER             5         // Minimum allowed step for sliding platform
#define PAN_STEPS_PER_DEGREE        78


// Positioning and speed default values
// In normal operation, these values will get overwritten by HTTP request
#define DEFAULT_SLIDE_TO_POS_SPEED  30.0
#define DEFAULT_SLIDE_TO_POS_ACCEL  60.0
#define DEFAULT_ROTATE_TO_POS_SPEED 30.0
#define DEFAULT_ROTATE_TO_POS_ACCEL 60.0


#define DEFAULT_HOMING_SPEED_SLIDE  DEFAULT_SLIDE_TO_POS_SPEED
#define DEFAULT_HOMING_SPEED_PAN    PAN_STEPS_PER_DEGREE


// Homing settings

typedef enum 
{ 
	SLIDER_FIRST = 0,
    SLIDER_MOTORS_OFF, 
    SLIDER_IDLE, 
    SLIDER_HOMING,
    SLIDER_MOVING_TO_START,
    SLIDER_MOVING_TO_END,
    SLIDER_READY,
    SLIDER_WORKING,
    SLIDER_LAST
} sliderState_t;


typedef enum
{
    HOMING_DIRECTION = 0,
    SLIDING_DIRECTION,
    PAN_DIRECTION,
    SLIDER_STEPS_PER_MM,
    ROTATION_STEPS_PER_DEG,
    HOMING_SPEED_SLIDE,
    HOMING_SPEED_PAN,
    MIN_SLIDER_STEP
} CameraSliderConfig_t;


typedef enum
{
    MOVE_RELATIVE = 0,
    MOVE_ABSOLUTE,
    MOVE_TO_STORED_POSITION_START,
    MOVE_TO_STORED_POSITION_END
} CameraSliderMovement_t;

#endif

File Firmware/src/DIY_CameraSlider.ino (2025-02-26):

#include <ESPmDNS.h>
#include <WiFiManager.h>
#include "WiFi.h"
#include "ESPAsyncWebServer.h"
#include "LittleFS.h"
#include <FlexyStepper.h>
#include "config_cameraslider.h"
#include "config_wifi.h"
#include "include/PersistSettings.h"

WiFiManager wifiManager;
AsyncWebServer server(80);

// We will use persistent storage to store our Camera Slider configuration
// but also allow us to edit it trough web/api
// This way we can decouple firmware from electronics/mech changes
// i.e We can change rail lenght or motor direction without recompiling firmware
// Note: You should not edit config below. Instead modify defaults inside `config_cameraslider.h`
struct SliderConfigStruct
{
    static const unsigned int Version = 1;

    uint16_t rail_length = RAIL_LENGTH_MM;
    uint16_t min_slider_step = MIN_STEP_SLIDER;


    int homing_direction = -1;  // Specify if we should reverse homing direction
    int slider_direction = 1;   // Increase (1) or decrease(-1) steps to get positive movement
    int rotate_direction = 1;   // Increase (1) or decrease(-1) steps to get positive movement

    uint16_t slide_steps_per_mm = SLIDE_STEPS_PER_MM;
    uint16_t pan_steps_per_degree = PAN_STEPS_PER_DEGREE;

    uint16_t homing_speed_slide = DEFAULT_HOMING_SPEED_SLIDE;
    uint16_t homing_speed_pan   = DEFAULT_HOMING_SPEED_PAN;

    float default_slider_speed = DEFAULT_SLIDE_TO_POS_SPEED;
    float default_slider_accel = DEFAULT_SLIDE_TO_POS_ACCEL;
    float default_rotate_speed = DEFAULT_ROTATE_TO_POS_SPEED;
    float default_rotate_accel = DEFAULT_ROTATE_TO_POS_ACCEL;
};

PersistSettings<SliderConfigStruct> SliderConfig(SliderConfigStruct::Version);

void setup()
{
    // Configure Serial communication
    Serial.begin(115200);
    delay(2000);
    Serial.setDebugOutput(true);
    Serial.println("DIY Camera Slider");

    WiFi.mode(WIFI_STA);

    WiFi.setHostname(MDNS_NAME);
    WiFi.setTxPower(WIFI_POWER_8_5dBm);

    int txPower = WiFi.getTxPower();
    Serial.print("TX power: ");
    Serial.println(txPower);

    delay(1000);

    // Peristent device config
    SliderConfig.Begin();
    if( SliderConfig.Valid() )
    {
        Serial.println("Reloading camera slider settings.");
    }
    else
    {
        Serial.println("Camera settings invalid. Resetting to default.");
    }

    // Configure and initialize GPIOs
	pinMode(PIN_LED, OUTPUT);
	pinMode(PIN_MTR_nRST, OUTPUT);
	pinMode(PIN_MTR_nEN, OUTPUT);
	pinMode(PIN_END_SWICH_X, INPUT_PULLUP);
	digitalWrite(PIN_LED, HIGH);
	digitalWrite(PIN_MTR_nRST, HIGH);
	digitalWrite(PIN_MTR_nEN, LOW);

	delay(1000);

	// Connect to WiFi
    bool res;
    res = wifiManager.autoConnect("SK-DIY-CameraSlider");

    wifiManager.setHostname(MDNS_NAME);
    wifiManager.setConnectRetries(4);

    if(!res) {
        Serial.println("Failed to connect or hit timeout");
        ESP.restart();
    }
    else {
        //if you get here you have connected to the WiFi
        Serial.println("Connected.");
    }

    // Initialize LittleFS
    Serial.print("Starting LittleFS...");
    if(!LittleFS.begin()){
        Serial.println("An Error has occurred while mounting LittleFS");
        return;
    }
    Serial.println("done.");

	Serial.print("WiFi IP: ");
	Serial.println(WiFi.localIP());

    if (!MDNS.begin(MDNS_NAME))
    {
        Serial.println("Error starting mDNS");
    }
    else
    {
        Serial.println((String) "mDNS http://" + MDNS_NAME + ".local");
    }

	// Setup motors
	setupMotors();
	CameraSlider_EnableMotors(true);
	digitalWrite(PIN_LED, LOW);

    // Initialize Web server
	setupWebServer();
	server.begin();

    // Debug message to signal we are initialized and entering loop
	Serial.println("Ready to go.");
}


void loop()
{
	while(1)
	{
		CameraSlider_tick();
	}
}

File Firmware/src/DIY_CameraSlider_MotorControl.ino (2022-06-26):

/*
CameraSlider - Motor Control
Description: This file contains all the functions we use to initialize, configure and control motors
*/

#include "config_cameraslider.h"
FlexyStepper stepper_slide;
FlexyStepper stepper_pan;

// Internal state variables
sliderState_t sliderState = SLIDER_IDLE;
bool bmotorState          = true;
bool bhomingComplete      = false;
float fSliderPos          = 0.0;
float fRotationPos        = 0.0;

// Start and stop positions
float fStartPos_Slider    = 0.0;
float fStartPos_Rotation  = 0.0;

float fEndPos_Slider      = 0.0;
float fEndPos_Rotation    = 0.0;

float fSlidingSpeed       = 0.0;
float fRotatingSpeed      = 0.0;

uint32_t slideDurationSec = 1;

// Main motor control function.
// We call this function from within our main loop to
// execute different commands based on current state
// of the CameraSlider state machine. Values/states of
// this state machine can be updated asynchronously (HTTP)
// or trough interrupts.
void CameraSlider_tick()
{
    switch(sliderState)
    {
        case SLIDER_MOTORS_OFF:
        break;

        case SLIDER_IDLE:
        break;

        case SLIDER_MOVING_TO_START:
            // Moving to start
            if((!stepper_slide.motionComplete()) || (!stepper_pan.motionComplete()))
            {
                stepper_slide.processMovement();
                stepper_pan.processMovement();
            }
            // Move complete
            else
            {
                if(slideDurationSec <=0 ) { slideDurationSec = 1; }

                // Calculate speed
                if(fEndPos_Slider >= fStartPos_Slider)
                {
                    fSlidingSpeed = (fEndPos_Slider - fStartPos_Slider) / slideDurationSec;
                }
                else
                {
                    fSlidingSpeed = (fStartPos_Slider - fEndPos_Slider) / slideDurationSec;
                }

                if(fEndPos_Rotation >= fStartPos_Rotation)
                {
                    fRotatingSpeed = (fEndPos_Rotation - fStartPos_Rotation) / (slideDurationSec);
                }
                else
                {
                    fRotatingSpeed = (fStartPos_Rotation - fEndPos_Rotation) / (slideDurationSec);
                }

                // Configure slider
                stepper_slide.setSpeedInMillimetersPerSecond(fSlidingSpeed);
                stepper_slide.setAccelerationInMillimetersPerSecondPerSecond(SliderConfig.Config.default_slider_accel);
                stepper_slide.setTargetPositionInMillimeters(fEndPos_Slider);

                // Configure pan
                stepper_pan.setSpeedInStepsPerSecond(fRotatingSpeed);
                stepper_pan.setAccelerationInStepsPerSecondPerSecond(SliderConfig.Config.default_slider_accel * SliderConfig.Config.pan_steps_per_degree);
                stepper_pan.setTargetPositionInSteps(fEndPos_Rotation);

                CameraSlider_SetState(SLIDER_MOVING_TO_END);
            }
        break;

        case SLIDER_MOVING_TO_END:
            // Moving to end position
            if((!stepper_slide.motionComplete()) || (!stepper_pan.motionComplete()))
            {
                stepper_slide.processMovement();
                stepper_pan.processMovement();
            }
            // Move completed
            else
            {
                CameraSlider_SetState(SLIDER_READY);
            }
            break;

        case SLIDER_HOMING:
            CameraSlider_HomeSlidingRail();
        break;

        case SLIDER_READY:
        break;

        case SLIDER_WORKING:
            if((!stepper_slide.motionComplete()) || (!stepper_pan.motionComplete()))
            {
                stepper_slide.processMovement();
                stepper_pan.processMovement();
            }
        break;

        default:
        return;
    }
}


void setupMotors()
{
    // Connect to motors
    stepper_slide.connectToPins(PIN_MOTOR_X_STEP, PIN_MOTOR_X_DIR);
    stepper_pan.connectToPins(PIN_MOTOR_Z_STEP, PIN_MOTOR_Z_DIR);

    // Configure sliding motor
    Serial.println("Slider motor");
    Serial.print("-- Steps per mm: ");
    Serial.println(SliderConfig.Config.slide_steps_per_mm, DEC);

    stepper_slide.setStepsPerMillimeter(SliderConfig.Config.slide_steps_per_mm);
    stepper_slide.setSpeedInMillimetersPerSecond(SliderConfig.Config.default_slider_speed * SliderConfig.Config.slide_steps_per_mm);
    stepper_slide.setAccelerationInMillimetersPerSecondPerSecond(SliderConfig.Config.default_slider_accel * SliderConfig.Config.slide_steps_per_mm);

    // Configure pan motor
    // -- Revolution in steps
    stepper_pan.setSpeedInStepsPerSecond(SliderConfig.Config.pan_steps_per_degree);
    stepper_pan.setAccelerationInStepsPerSecondPerSecond(SliderConfig.Config.default_slider_accel * SliderConfig.Config.pan_steps_per_degree);

}

void CameraSlider_MoveToPositionRelative(float xPos, float xSpeed, float xAccel, float rAngle, float rSpeed, float rAccel)
{
    // Invert slider or pan motor if necessary
    xPos = SliderConfig.Config.slider_direction * xPos;
    rAngle = SliderConfig.Config.rotate_direction * rAngle;

    // Setup slider
    stepper_slide.setTargetPositionInMillimeters(xPos);
    stepper_slide.setSpeedInMillimetersPerSecond(xSpeed);
    stepper_slide.setAccelerationInMillimetersPerSecondPerSecond(xAccel);

    // Setup pan
    stepper_pan.setTargetPositionRelativeInSteps(rAngle * SliderConfig.Config.pan_steps_per_degree);
    stepper_pan.setSpeedInStepsPerSecond(rSpeed * SliderConfig.Config.pan_steps_per_degree);
    stepper_pan.setAccelerationInStepsPerSecondPerSecond(rAccel * SliderConfig.Config.pan_steps_per_degree);

    // Updatestate machine
    sliderState = SLIDER_WORKING;
}

void CameraSlider_MoveToPositionAbsolute(float xPos, float xSpeed, float xAccel, float rSteps, float rSpeed, float rAccel)
{
    // Invert slider or pan motor if necessary
    xPos = SliderConfig.Config.slider_direction * xPos;
    rSteps = SliderConfig.Config.rotate_direction * rSteps;

    // Setup slider
    stepper_slide.setTargetPositionInMillimeters(xPos);
    stepper_slide.setSpeedInMillimetersPerSecond(xSpeed);
    stepper_slide.setAccelerationInMillimetersPerSecondPerSecond(xAccel);

    // Setup pan
    stepper_pan.setTargetPositionInSteps(rSteps);
    stepper_pan.setSpeedInStepsPerSecond(rSpeed * SliderConfig.Config.pan_steps_per_degree);
    stepper_pan.setAccelerationInStepsPerSecondPerSecond(rAccel * SliderConfig.Config.pan_steps_per_degree);

    // Updatestate machine
    sliderState = SLIDER_WORKING;
}

void CameraSlider_MoveToStart(float xSpeed, float xAccel, float rSpeed, float rAccel)
{
    CameraSlider_MoveToPositionAbsolute(fStartPos_Slider, xSpeed, xAccel, fStartPos_Rotation, rSpeed, rAccel);
}

void CameraSlider_MoveToEnd(float xSpeed, float xAccel, float rSpeed, float rAccel)
{
    CameraSlider_MoveToPositionAbsolute(fEndPos_Slider, xSpeed, xAccel, fEndPos_Rotation, rSpeed, rAccel);
}
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

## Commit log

2022-06-26 Initial commit.
    [01_Top.SchDoc, 02_Power.SchDoc, 03_MCU.SchDoc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]
2022-07-23 Fixing BoM issues as per open issue #2.
2022-07-23 Adding limit switch to the BoM.
2022-08-09 Updating MFG release/gerbers to reflect correct layout.
    [OpenCameraSlider_PCB.GBL, OpenCameraSlider_PCB.GBO, OpenCameraSlider_PCB.GBP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]
2025-02-26 Updating libraries refs. Switching from SPIFS to LittleFS.
